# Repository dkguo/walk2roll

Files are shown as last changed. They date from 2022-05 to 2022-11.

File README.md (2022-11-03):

<h1 align="center">
Leg Shaping and Event-Driven Control of a Small-Scale, Low-DoF, Two-Mode Robot
</h1>

<div align="center">
<h3>
<a href="https://dkguo.com">Dingkun Guo</a>,
Larissa Wermers, and
<a href="https://me.engin.umich.edu/people/faculty/kenn-oldham/">Kenn R. Oldham</a>
<br>
<br>
IEEE/ASME Transactions on Mechatronics, 2022
<br>
<br>
IEEE/ASME International Conference on Advanced Intelligent Mechatronics (AIM), 2022
<br>
<br>
<a href="https://dkguo.com/research/walk2roll">[Website]</a>
<a href="https://arxiv.org/pdf/2205.14579.pdf">[Paper]</a>
<a href="https://youtu.be/P6FxYMbSkI4"> [Presentation]</a>
<br>
</h3>
<br>
<p align="center">
rolling
walking
transition
</p>
<br>
</div>

# Citation
Please cite this work if it helps your research:

```
@ARTICLE{walk2roll,  
  author={Guo, Dingkun and Wermers, Larissa and Oldham, Kenn R.},
  journal={IEEE/ASME Transactions on Mechatronics}, 
  title={Leg Shaping and Event-Driven Control of a Small-Scale, Low-DoF, Two-Mode Robot}, 
  year={2022}, volume={27}, number={4}, pages={1910-1918},
  doi={10.1109/TMECH.2022.3173183}}
```

# Overview
In this work, we design and prototype a two-DoF walking-rolling robot. This repository contains
1) Code for leg profile generation and analysis
2) CAD files of the prototype
3) Code of the event-driven controller

# Prerequisites
This code is tested with MATLAB, Arduino, and Arduino UNO Wifi Rev 2.

# Leg profile generation and analysis
In `design` foler:
1. The MATLAB file to randomly generate leg profiles and calculate J1 and J2 will be added by request. A `.mat` file that contains the raw data from the Monte Carlo simulations is provided [here](https://drive.google.com/file/d/1t3DsJioSSCW6Dw8d_Bq3EJVaL-_BnXOD/view?usp=sharing). You can load it first and run the remaining files.
2. Run `a_CriteriaPlots.m`, `b_CleanTrends.m`, `c_ApproximateParetoCurve.m` sequentially to generate figures in the paper.

<p float="left">
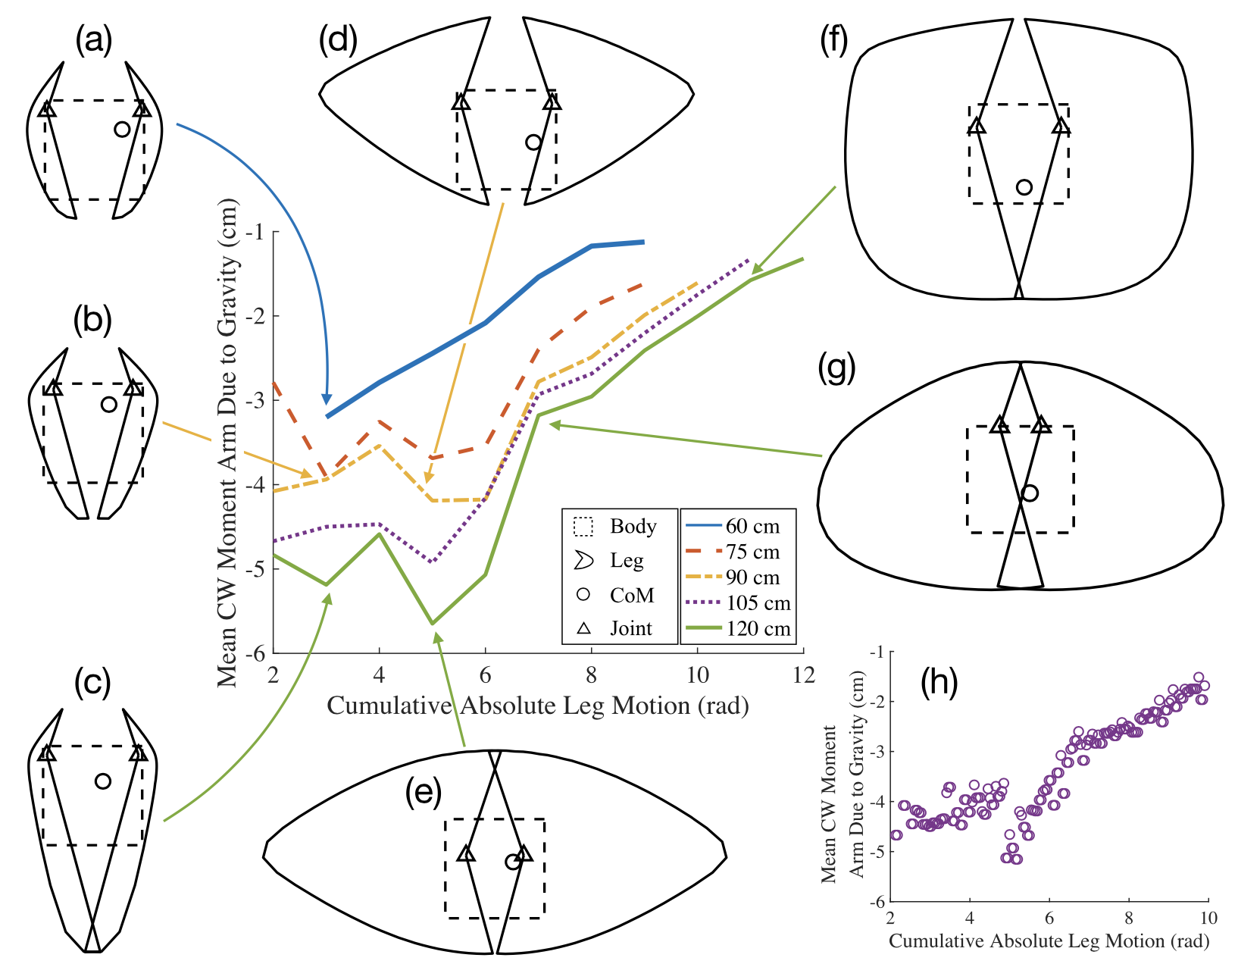
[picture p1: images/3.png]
design trend

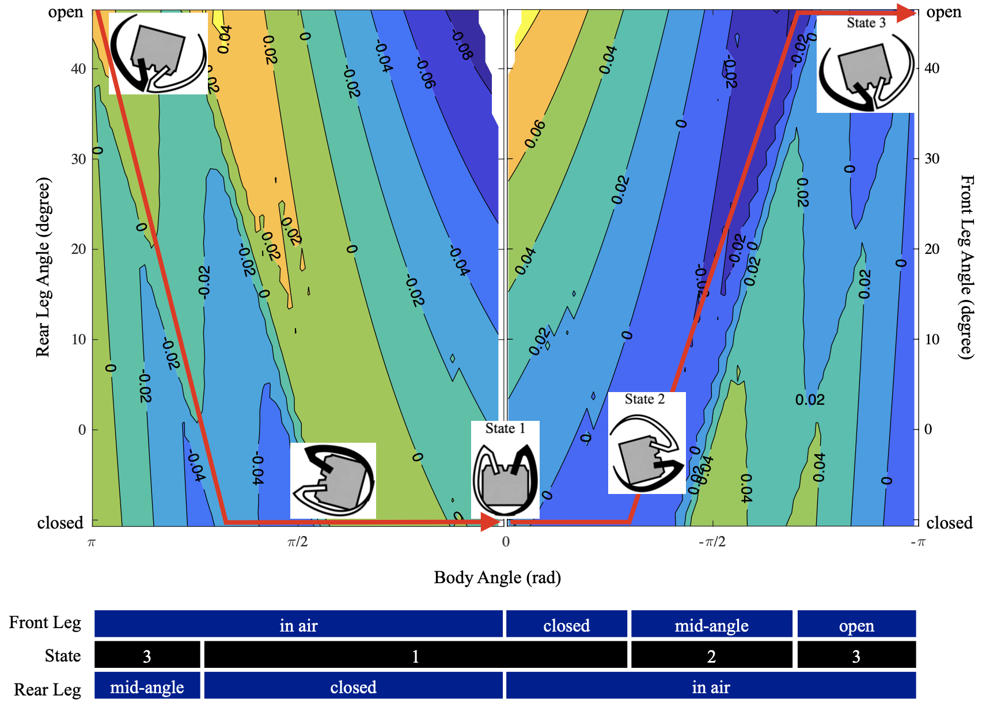
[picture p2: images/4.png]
design contour

</p>

# CAD
CAD files used for 3D printing the robot are included in `CAD` folder.

<p float="left">
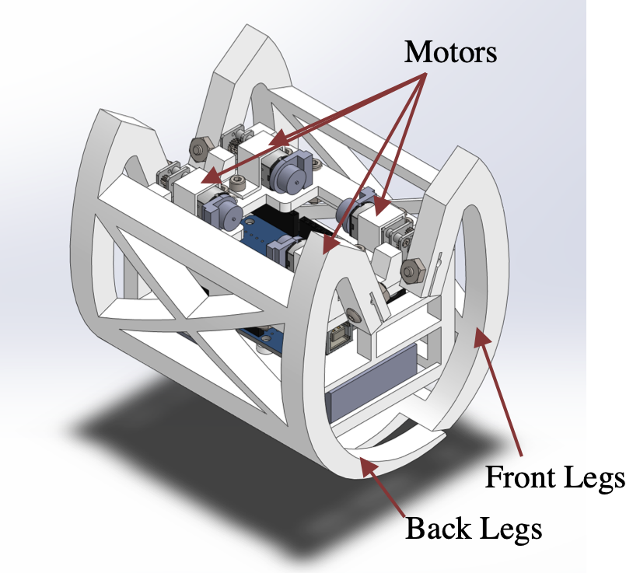
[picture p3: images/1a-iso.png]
CAD iso

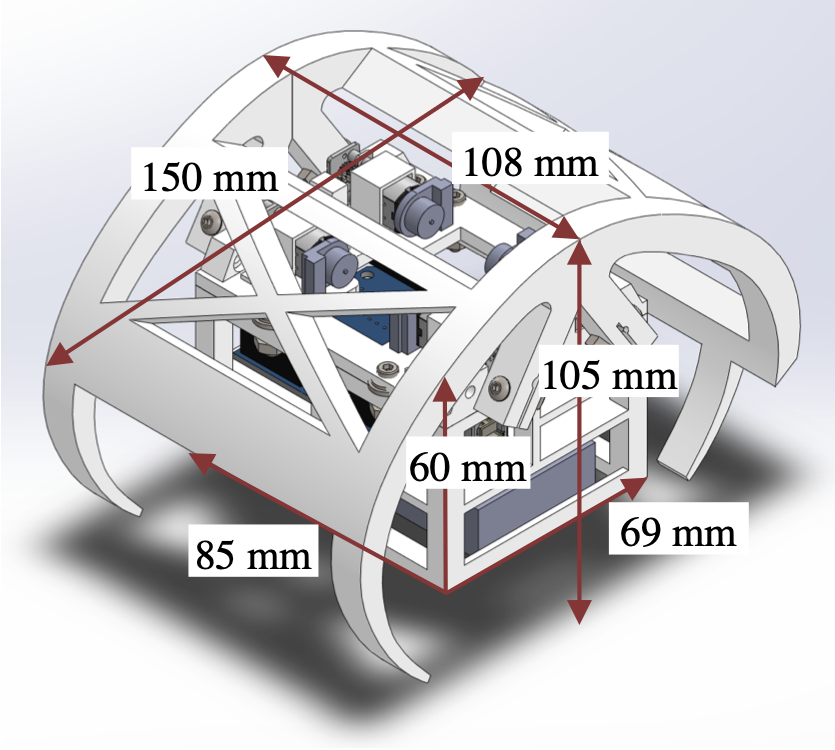
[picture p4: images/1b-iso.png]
CAD

</p>

# Event-driven controller
An electrical diagram for the robot is shown below:

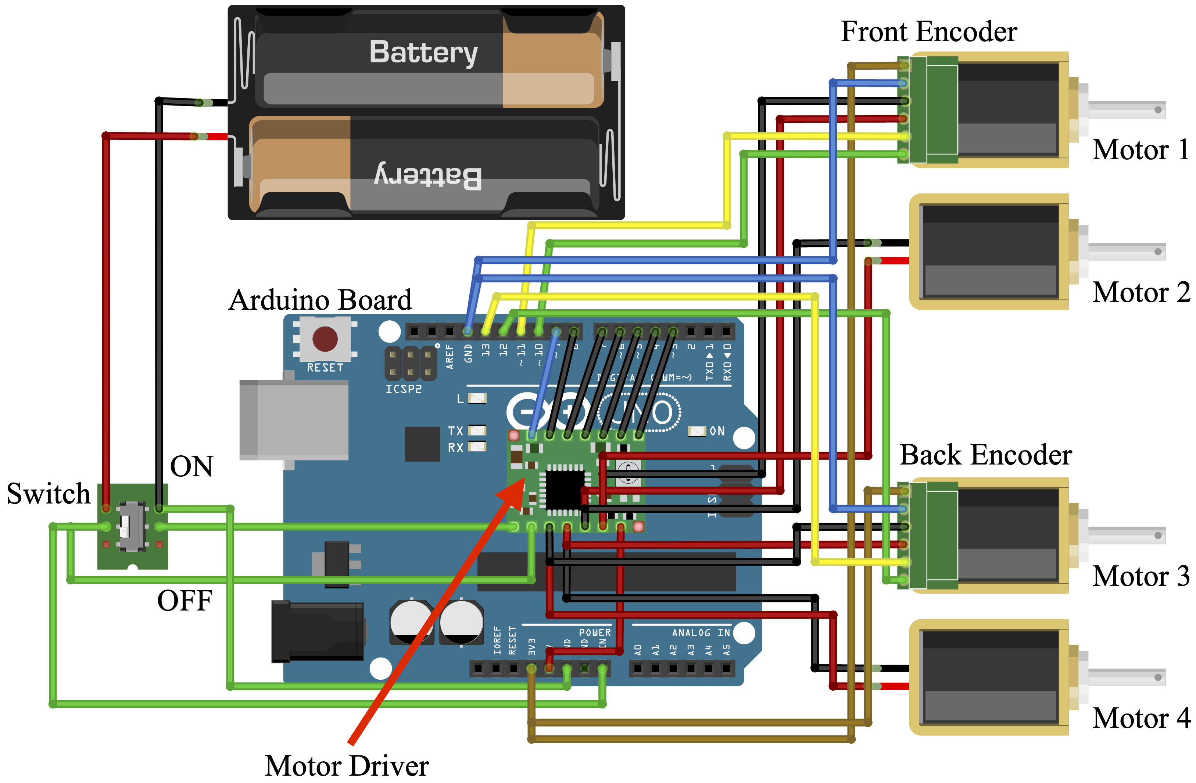
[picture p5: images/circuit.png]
Electrical Diagram


In `controller` folder, compile and upload `roll.ino`, `walk.ino`, or `roll_and_walk.ino` to Arduino board and the robot is alive!

Note: The definitions of front and rear legs are opposite to those in the paper. The state numbers are also different.

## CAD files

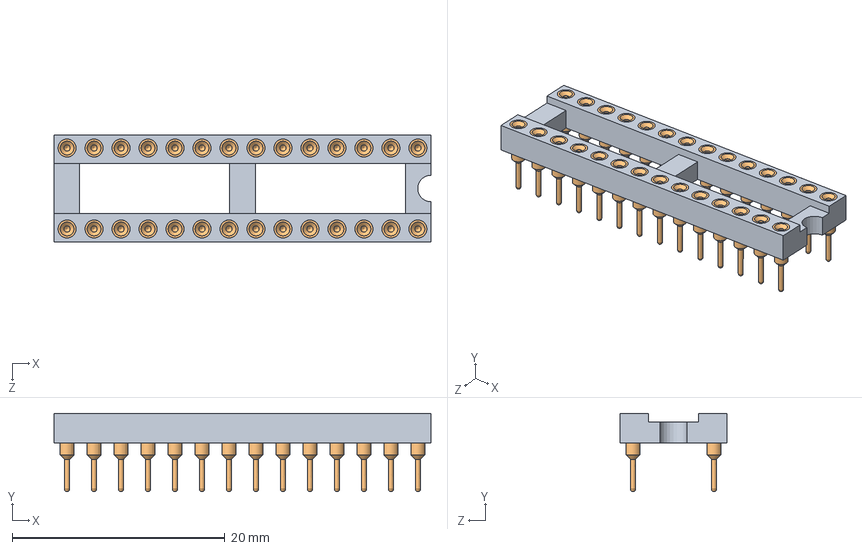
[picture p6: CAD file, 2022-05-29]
CAD/Arduino/Dip28 Montaj.SLDASM
35.5 x 7.37 x 10.1 mm
dip28
dip socket pin x 28

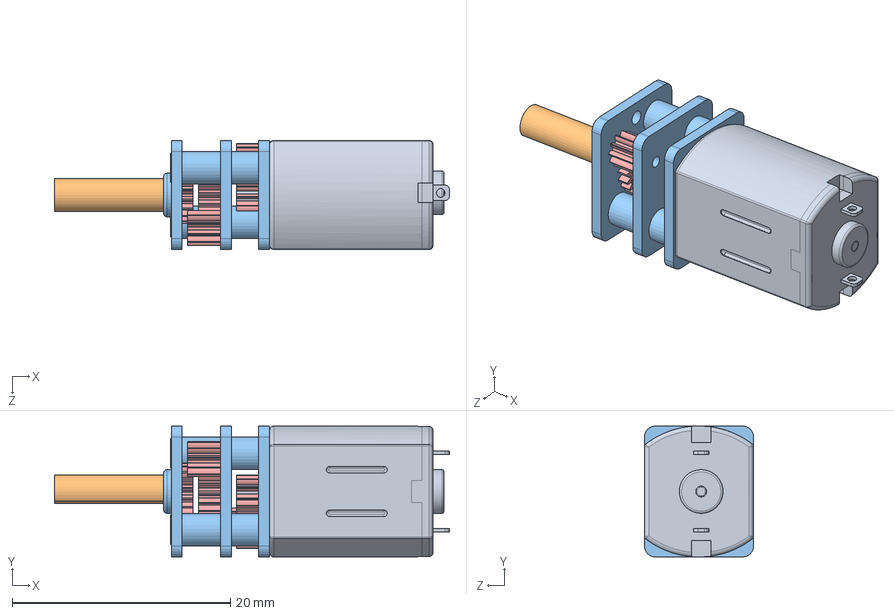
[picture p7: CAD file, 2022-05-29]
CAD/motor/n20 motor.SLDASM
36.2 x 12.0 x 10.0 mm
motor
n20_shaft
n20_gearbox
cross recessed countersunk head screws gb1 x 2
spur gear_gb x 6

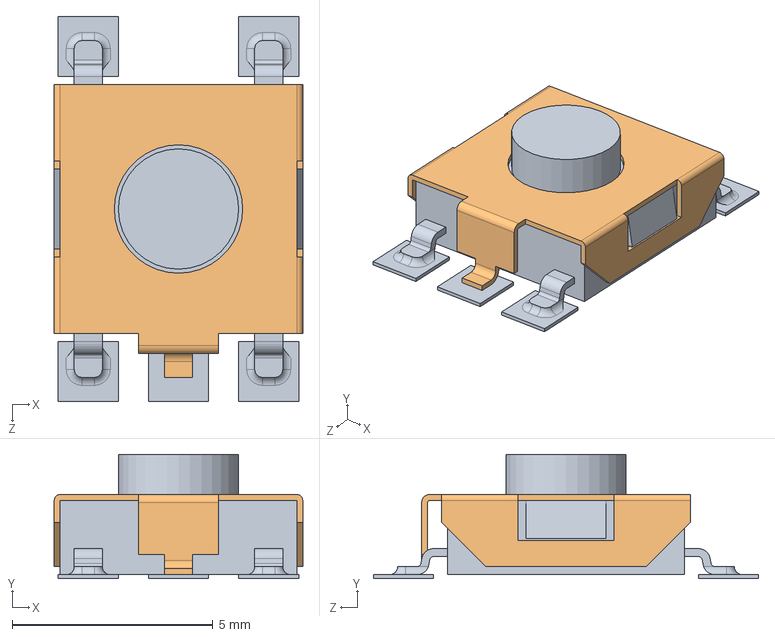
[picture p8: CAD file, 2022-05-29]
CAD/Arduino/RESET Montaj.SLDASM
6.20 x 3.10 x 9.60 mm
RESET CORE
RESET

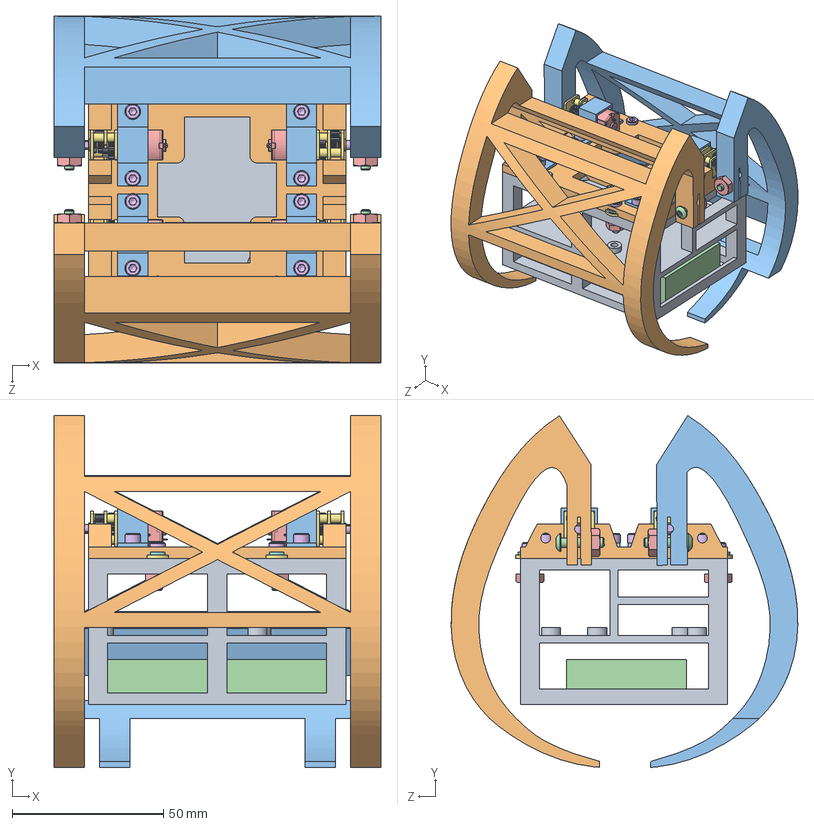
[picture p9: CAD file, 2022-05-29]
CAD/Assemble.SLDASM
108.0 x 116.4 x 114.6 mm
Chamber
Lid
Motor Mounts x 4
Battery Holder
motor x 4
n20_shaft x 4
n20_gearbox x 4
cross recessed countersunk head screws gb1 x 8
spur gear_gb x 24
front leg
back leg
socket button head cap screw_ai x 4
machine screw nut hex_ai x 10
socket head cap screw_ai x 12
flat washer type a narrow_ai x 4
flat washer type a selected narrow_ai x 4

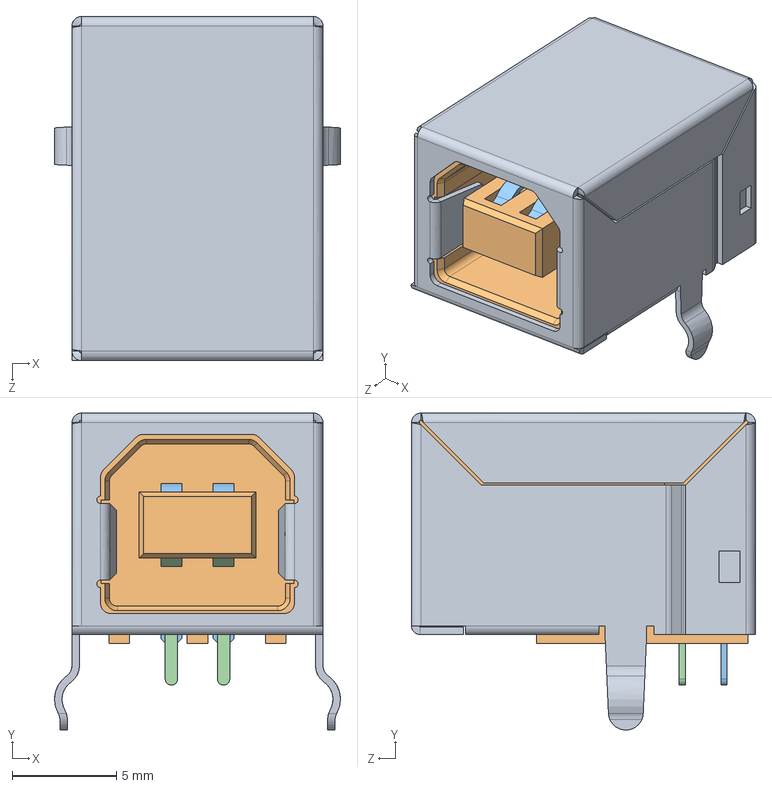
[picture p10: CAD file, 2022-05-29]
CAD/Arduino/USB Montaj.SLDPRT.SLDASM
13.7 x 15.2 x 16.5 mm
USB SHELL
USB core
usb top contact x 2
usb btm contact x 2

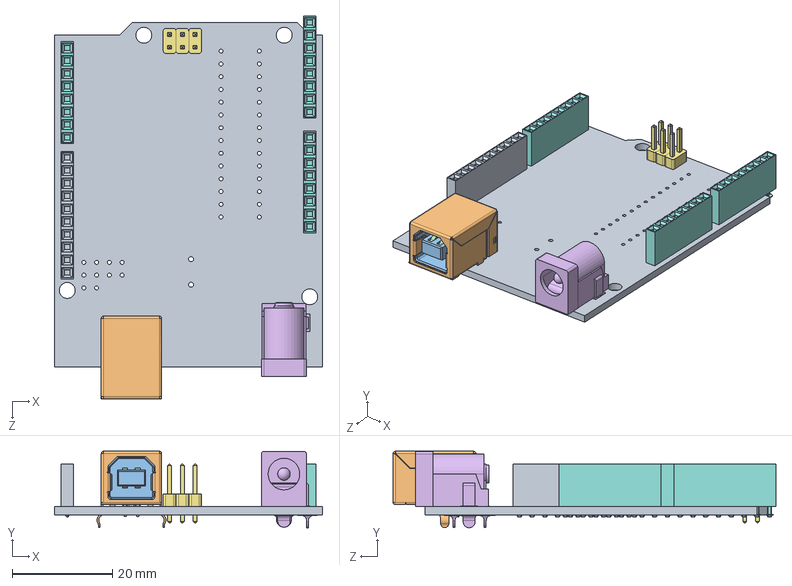
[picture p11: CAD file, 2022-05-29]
CAD/Arduino/Arduino UNO R3 Montaj.SLDASM
53.3 x 15.2 x 76.2 mm
unoboard blue
USB SHELL
USB core
usb top contact x 2
usb btm contact x 2
power jack
2pin_header__02 x 3
8 PORT HEADER x 3
10 PORT HEADER

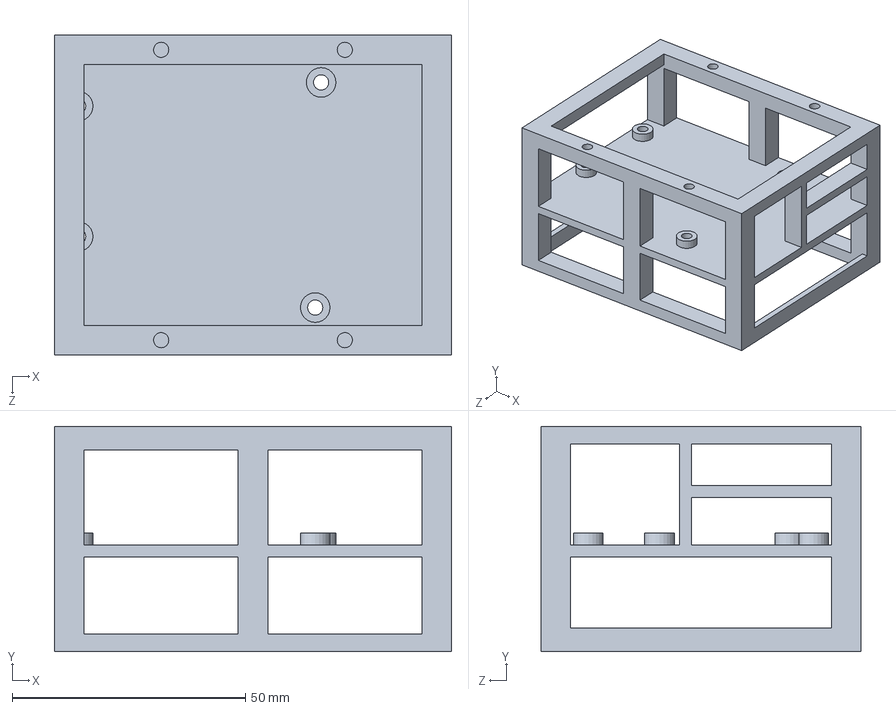
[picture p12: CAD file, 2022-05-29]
CAD/Chamber.SLDPRT
85.1 x 48.3 x 68.6 mm

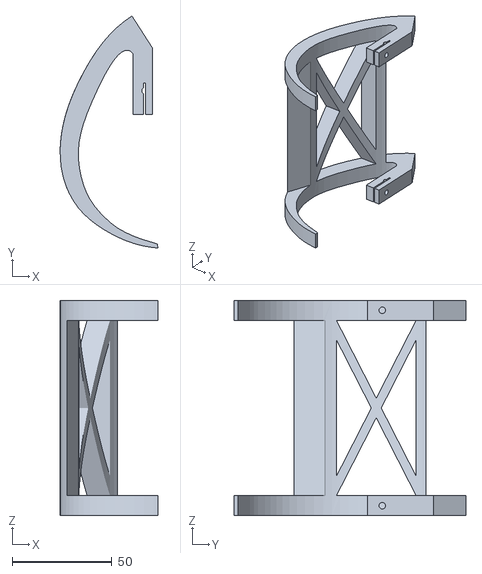
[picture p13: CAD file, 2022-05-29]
CAD/for print/front leg.STL
49.0 x 116.3 x 108.0

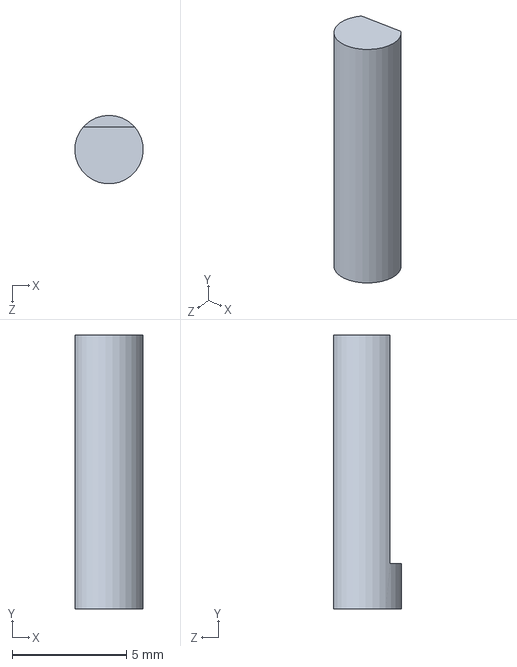
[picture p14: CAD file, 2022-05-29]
CAD/motor/n20_shaft.SLDPRT
3.00 x 12.0 x 2.99 mm

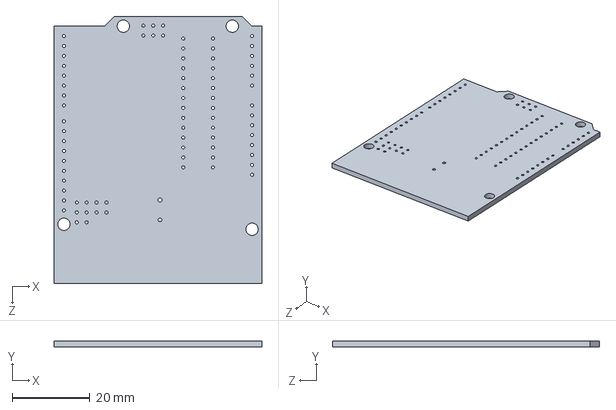
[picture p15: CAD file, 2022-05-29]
CAD/Arduino/unoboard blue.SLDPRT
53.3 x 1.65 x 68.6 mm

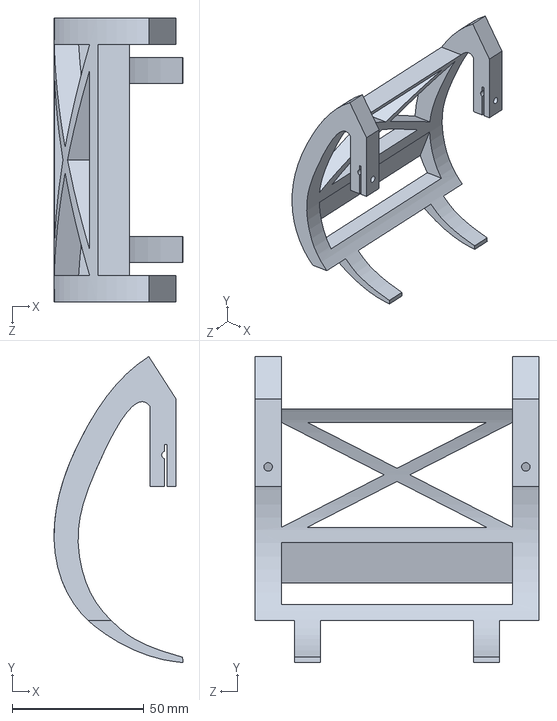
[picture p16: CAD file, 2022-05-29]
CAD/back leg.SLDPRT
49.0 x 116.3 x 108.0 mm

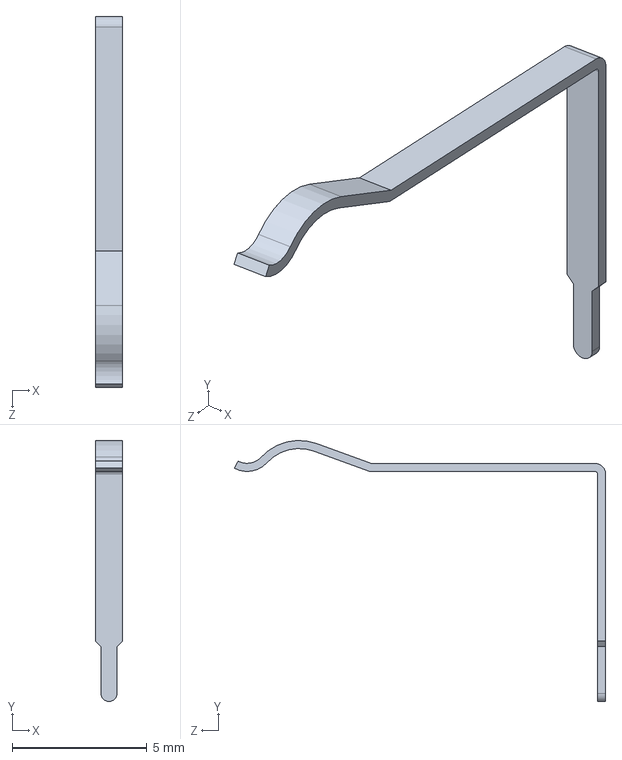
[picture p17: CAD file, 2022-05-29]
CAD/Arduino/usb top contact.SLDPRT
1.00 x 9.67 x 13.8 mm

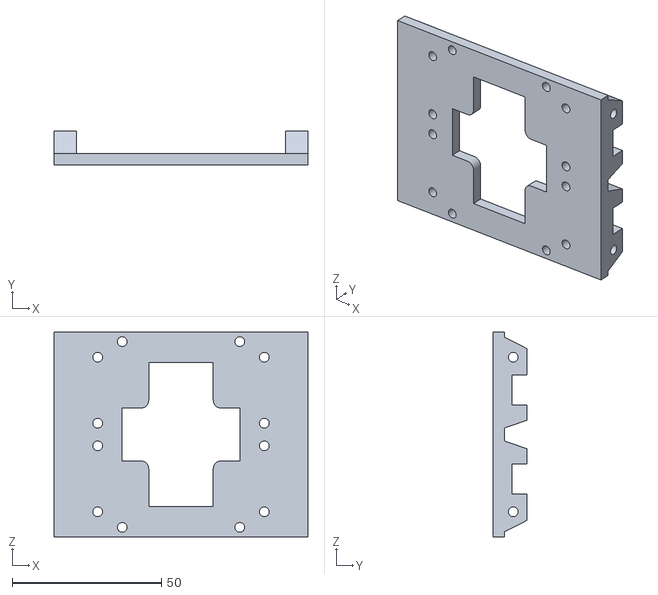
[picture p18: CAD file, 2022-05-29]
CAD/for print/Lid.STL
85.1 x 11.4 x 68.6

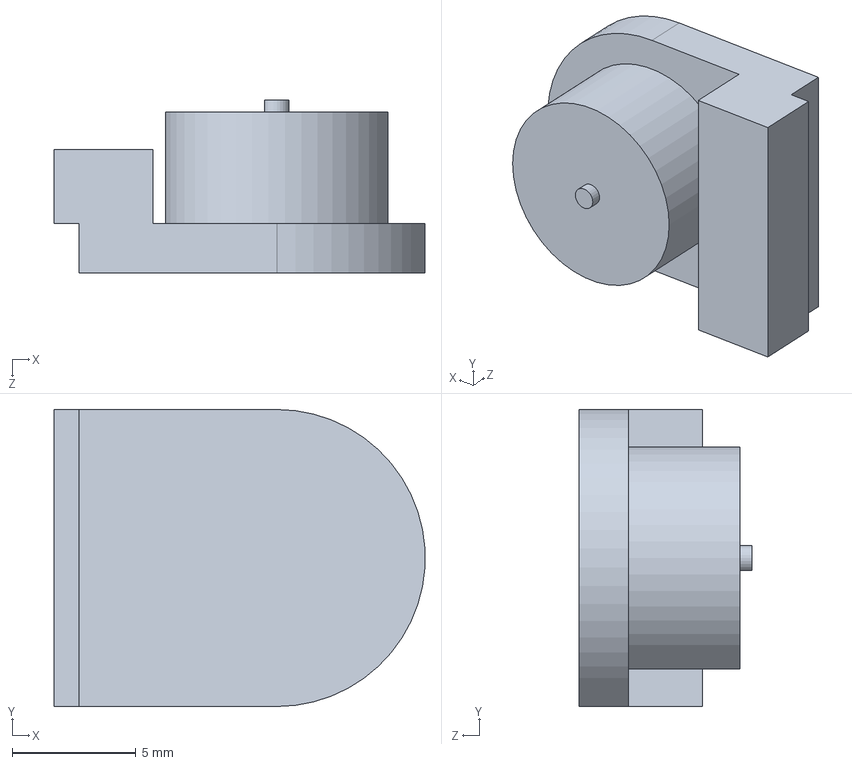
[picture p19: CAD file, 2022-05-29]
CAD/motor/encoder.SLDPRT
15.0 x 12.0 x 7.00 mm

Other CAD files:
CAD/motor/motor.SLDASM
CAD/for print/Chamber.STL
CAD/number 4 quarter inch.SLDPRT
CAD/Arduino/PADS001.SLDPRT
CAD/Arduino/10 PORT HEADER.SLDPRT
CAD/Arduino/2pin_header__02.sldprt
CAD/Arduino/47uf CAP Dcase.SLDPRT
CAD/Arduino/8 PORT HEADER.SLDPRT
CAD/Arduino/ATMEL328P.SLDPRT
CAD/Arduino/RESET CORE.SLDPRT
CAD/Arduino/RESET.SLDPRT
CAD/Arduino/USB SHELL.SLDPRT
CAD/Arduino/USB core.SLDPRT
CAD/Arduino/blm21.SLDPRT
CAD/Arduino/crystal.sldprt
CAD/Arduino/dip socket pin.SLDPRT
CAD/Arduino/dip28.SLDPRT
CAD/Arduino/m7 diode.SLDPRT
CAD/Arduino/nano - reg.SLDPRT
CAD/Arduino/power jack.SLDPRT
CAD/Arduino/usb btm contact.SLDPRT
CAD/Assemble.SLDDRW
CAD/Battery Holder.SLDPRT
CAD/Lid.SLDPRT
CAD/Motor Mounts.SLDPRT
CAD/Quarter nut.SLDPRT
CAD/for print/back leg.STL
CAD/front leg.SLDPRT
CAD/leg profile.SLDDRW
CAD/motor/motor.SLDPRT
CAD/motor/n20_gearbox.SLDPRT
CAD/number 4 screw half inch.SLDPRT

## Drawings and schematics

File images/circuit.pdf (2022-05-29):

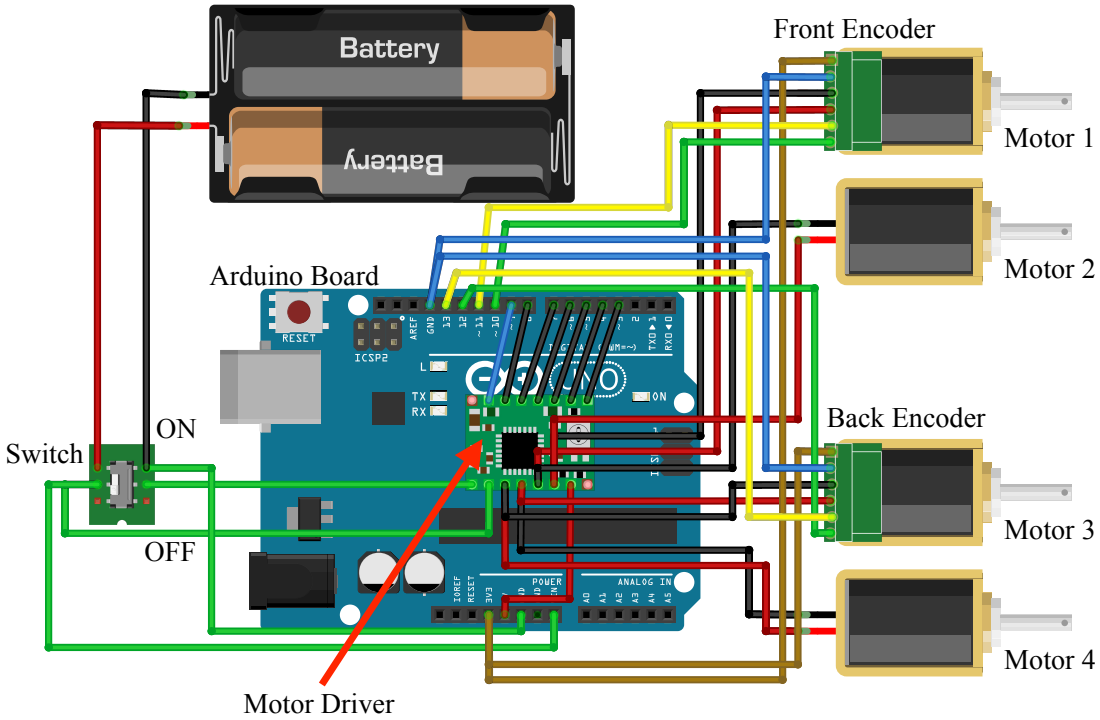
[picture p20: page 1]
Motor 1; Motor 2; Motor 3; Motor 4; Front Encoder; Back Encoder; Switch; OFF; Motor Driver; Arduino Board

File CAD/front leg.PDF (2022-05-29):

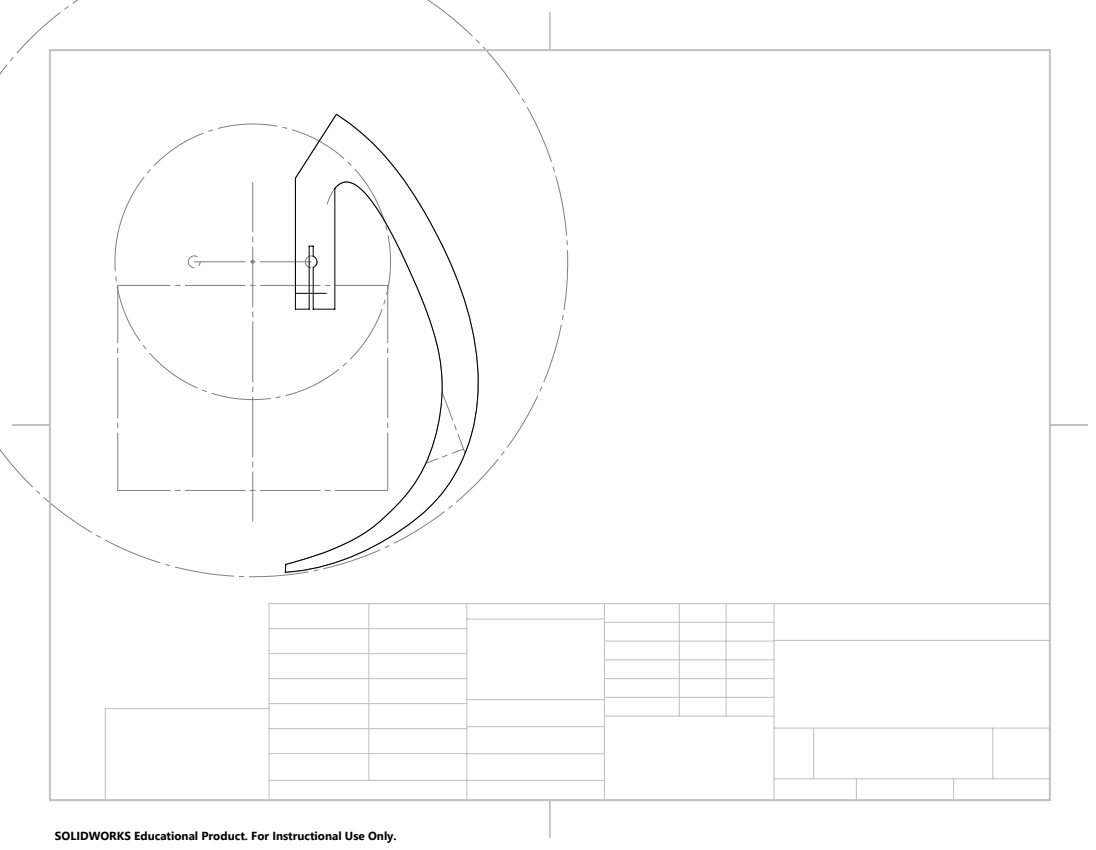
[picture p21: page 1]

SOLIDWORKS Educational Product. For Instructional Use Only.

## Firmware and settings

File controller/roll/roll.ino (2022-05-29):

//
// roll
//
// Robotics Research with Prof. Oldham
//
// Created by Dingkun Guo
// Copyright © 2022 dkguo. All rights reserved.
//

#include <Arduino_LSM6DS3.h>

// Connections for motor driver
const int PWMB = 9;
const int BIN2 = 8;
const int BIN1 = 7;
const int STBY = 6;
const int AIN1 = 5;
const int AIN2 = 4;
const int PWMA = 3;

// Connections for encoders
const int front_encoderA = 13;
const int front_encoderB = 12;
const int back_encoderA = 10;
const int back_encoderB = 11;

const float SUPPLY_VOLTAGE = 5;

unsigned long execution_duration = 0;
unsigned long last_execution_time = 0;
unsigned long timer = 0;

// for encoder
float f_Ep, f_Ei = 0, f_Ed;
float b_Ep, b_Ei = 0, b_Ed;
int front_pos = 0;
int back_pos = 0;

// PID controller
float Kp = 0.03;
float Ki = 0.02;
float Kd = 0.001;

int state = 0;
int prev_state = 0;

int front_des = 0;
int back_des = 0;

float acc_x, acc_y, acc_z;
float gyr_x, gyr_y, gyr_z;


void setup() {
  pinMode(back_encoderA, INPUT);
  pinMode(back_encoderB, INPUT);
  pinMode(front_encoderA, INPUT);
  pinMode(front_encoderB, INPUT);

  pinMode(STBY, OUTPUT);
  pinMode(AIN1, OUTPUT);
  pinMode(AIN2, OUTPUT);
  pinMode(PWMA, OUTPUT);
  pinMode(BIN1, OUTPUT);
  pinMode(BIN2, OUTPUT);
  pinMode(PWMB, OUTPUT);

  Serial.begin(9600);
  while (!Serial);

  if (!IMU.begin()) {
    Serial.println("Failed to initialize IMU!");
    while (1);
  }

  Serial.println("-------------------------------------");

  attachInterrupt(digitalPinToInterrupt(back_encoderA), isrBA, CHANGE); 
  attachInterrupt(digitalPinToInterrupt(back_encoderB), isrBB, CHANGE);
  attachInterrupt(digitalPinToInterrupt(front_encoderA),isrFA, CHANGE); 
  attachInterrupt(digitalPinToInterrupt(front_encoderB), isrFB, CHANGE);
}

void loop() {
  execution_duration = micros() - last_execution_time;
  last_execution_time = micros();
  if (state != prev_state) {
    timer = 0;
    prev_state = state;
  }
  timer += execution_duration;

  IMU.readAcceleration(acc_x, acc_y, acc_z);
  IMU.readGyroscope(gyr_x, gyr_y, gyr_z);

  switch (state) {
    case 0:
      front_des = 0;
      back_des = 0;
      if (acc_y < -0.4 && acc_z < 0.9)
        state = 2;
      else if (acc_z > 0 && front_pos > -25 && front_pos < 25 && back_pos > -25 && back_pos < 25)
        state = 3;
      else if (acc_z < -0.9 && front_pos > -25 && front_pos < 25 && back_pos > -25 && back_pos < 25)
        state = 4;
      break;

    case 2:
      front_des = 0;
      back_des = 600;
      if (timer > 500000 && back_pos > 550 && acc_y > 0.2)
        state = 3;
      else if (timer > 1000000 && back_pos > 550)
        state = 4;
      break;

    case 3:
      front_des = 1500;
      back_des = 300;
      
      if (back_pos > 250 && acc_y < -0.98)
        state = 4;
      else if (timer > 1000000 && back_pos > 250)
        state = 0;
      break;

    case 4:
      front_des = 1500;
      back_des = 1300;
      if (back_pos > 1250 && acc_y > 0.1 && acc_z < -0.9)
        state = 0;
      else if (timer > 1000000 && back_pos > 1250 && acc_y < -0.4 && acc_z > -0.98)
        state = 5;
      else if (timer > 1000000 && back_pos > 1250 && acc_z > 0.99)
        state = 0;
      break;

    case 5:
      front_des = 1500;
      if (timer < 500000)
        back_des = 700;
      else
        back_des = 0;

      if (back_pos < 50 && acc_y < -0.98 && acc_z > -0.99)
        state = 4;
      else if (back_pos < 50 && acc_y > -0.4 && acc_z > 0.9)
        state = 0;
      break;
  }

  int front_pwm = front_leg_to(front_des);
  int back_pwm = back_leg_to(back_des);

  // print out info
  Serial.print(state);
  Serial.print('\t');
  Serial.print(front_des);
  Serial.print('\t');
  Serial.print(back_des);
  Serial.print('\t');
  Serial.print(front_pos);
  Serial.print('\t');
  Serial.print(back_pos);
  Serial.print('\t');
  Serial.print(front_pwm);
  Serial.print('\t');
  Serial.print(back_pwm);
  Serial.print('\t');
  Serial.print(acc_y);
  Serial.print('\t');
  Serial.print(acc_z);
  Serial.print('\t');
  Serial.print(gyr_x);
  Serial.print('\n');
}


// -----------------Leg PID controller----------------
int front_leg_to(const int p) {
  f_Ep = p - front_pos;
  f_Ei += f_Ep * (float) execution_duration / 1000000;
  f_Ed = 0; // - motor_velocity;
  
  float voltage = Kp * f_Ep + Ki * f_Ei + Kd * f_Ed;

  int motor = int(abs(voltage * 255 / SUPPLY_VOLTAGE));
  if (motor > 150) {
    motor = 150;
    f_Ei -= f_Ep * (float) execution_duration / 1000000;
  }

  if (voltage >= 0) 
    front_leg_forward(motor);
  else 
    front_leg_backward(motor);

  return motor;
}


int back_leg_to(const int p) {
  b_Ep = p - back_pos;
  b_Ei += b_Ep * (float) execution_duration / 1000000;
  b_Ed = 0; // - motor_velocity;
  
  float voltage = Kp * b_Ep + Ki * b_Ei + Kd * b_Ed;

  int motor = int(abs(voltage * 255 / SUPPLY_VOLTAGE));
  if (motor > 150) {
    motor = 150;
    b_Ei -= b_Ep * (float) execution_duration / 1000000;
  }

  if (voltage >= 0) 
    back_leg_forward(motor);
  else 
    back_leg_backward(motor);

  return motor;
}


// -----------------Leg position----------------
void front_leg_forward(int m) {
  digitalWrite(STBY, HIGH);
  digitalWrite(BIN1, HIGH);
  digitalWrite(BIN2, LOW);
  analogWrite(PWMB, m);
}

void front_leg_backward(int m) {
  digitalWrite(STBY, HIGH);
  digitalWrite(BIN1, LOW);
  digitalWrite(BIN2, HIGH);
  analogWrite(PWMB, m);
}

void back_leg_backward(int m) {
  digitalWrite(STBY, HIGH);
  digitalWrite(AIN1, LOW);
  digitalWrite(AIN2, HIGH);
  analogWrite(PWMA, m);
}

void back_leg_forward(int m) {
  digitalWrite(STBY, HIGH);  
  digitalWrite(AIN1, HIGH);
  digitalWrite(AIN2, LOW);
  analogWrite(PWMA, m);
}


// ---------------Encoder Interrupts----------------
// interrupt routine for encoders
void isrFA() {
  int f_channelA = digitalRead(front_encoderA); 
  int f_channelB = digitalRead(front_encoderB); 
  if (f_channelA == f_channelB) 
    --front_pos;
  else 
    ++front_pos;
}

void isrBA() {
  int b_channelA = digitalRead(back_encoderA); 
  int b_channelB = digitalRead(back_encoderB); 
  if (b_channelA == b_channelB) 
    --back_pos;
  else 
    ++back_pos;
}

void isrFB() {
  int f_channelA = digitalRead(front_encoderA); 
  int f_channelB = digitalRead(front_encoderB); 
  if (f_channelA == f_channelB)
    ++front_pos;
  else
    --front_pos;
}

void isrBB() {
  int b_channelA = digitalRead(back_encoderA); 
  int b_channelB = digitalRead(back_encoderB); 
  if (b_channelA == b_channelB) 
    ++back_pos;
  else
    --back_pos;
}

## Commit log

2022-05-29 release code
    [10 PORT HEADER.SLDPRT, 2pin_header__02.sldprt, 47uf CAP Dcase.SLDPRT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]
2022-05-29 add cad images
